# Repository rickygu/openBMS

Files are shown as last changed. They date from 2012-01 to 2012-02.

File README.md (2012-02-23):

Intro
===========

**openBMS is seeking contributors**

Offical Development Google Group: http://groups.google.com/group/openbms

openBMS is an electric vehicle lithium ion battery management system(BMS) based on the [Linear Tech LTC6802-2](http://www.linear.com/product/LTC6802-2) integrated IC and [Cinch ModICE](http://www.cinch.com/products/transportation/modular-integrated-connector-enclosure) automotive enclosure. 

This BMS was originally designed by Ricky Gu of [UBC Electric Car Club](http://ubcecc.com) for the eBeetle project in spring 2010. The eBeetle became the [first electric vehicle to drive coast to coast across Canada](http://www.wired.com/autopia/2010/09/electrified-beetle-goes-coast-to-coast-in-canada/) in summer 2010. This BMS was one of the key component that enabled the eBeetle to drive 6400km in 14 days. 

Todo
==========
* Complete Arduino breakout board to interface with BMS boards
* Start Wiki Documentations

Master Board Features
===============

* Arduino Micro-controller
* Low Voltage Protection
* High Voltage Protection
* LCD Display
* Hall Effect Isolated Current Sensor
* Coulomb Counting

Daughter Board Features
===========

* Measures up to 12 Li-Ion Cells in Series (60V Max)
* Stackable Architecture Enables >1000V Systems
* 0.25% Maximum Total Measurement Error
* 13ms to Measure All Cells in a System
* Cell Balancing:
* On-Chip Passive Cell Balancing
* Two Thermistor Inputs Plus On-Board Temperature Sensor
* 1MHz Daisy-Chainable Serial Interface
* High EMI Immunity
* Delta Sigma Converter with Built-In Noise Filter
* Open Wire Connection Fault Detection
* Low Power Modes

Mechanical Features
===========
* Interfaces with Cinch SHS Harness Connector
* Header modularity and blank headers offer design flexibility for alternate interconnects
* Simple Assembly
* Slide Header/PCB assembly in the Enclosure and snap shut
* Housings – Glass filled polymer
* Pins – Brass – Post tin plated
* Seals – Silicone elastomer
* RoHS – Compliant
* Operating Temperature -55oC to +85oC
* Sealing IP67, IP69K
* Current Cycling 500 Hr
* Salt Fog 96 Hr
* Thermal Shock 10 cycles
* Vibration 10 to 2000 Hz – 20 g peak level – XYZ – 24 Hr
* Shock 50 g – 20 pulses
* Temperature Humidity 1008 Hr
* Temperature Life 1000 Hr
* UV exposure 1000 Hr
* Resists to most fluids used in industrial applications
  
Photos
===========
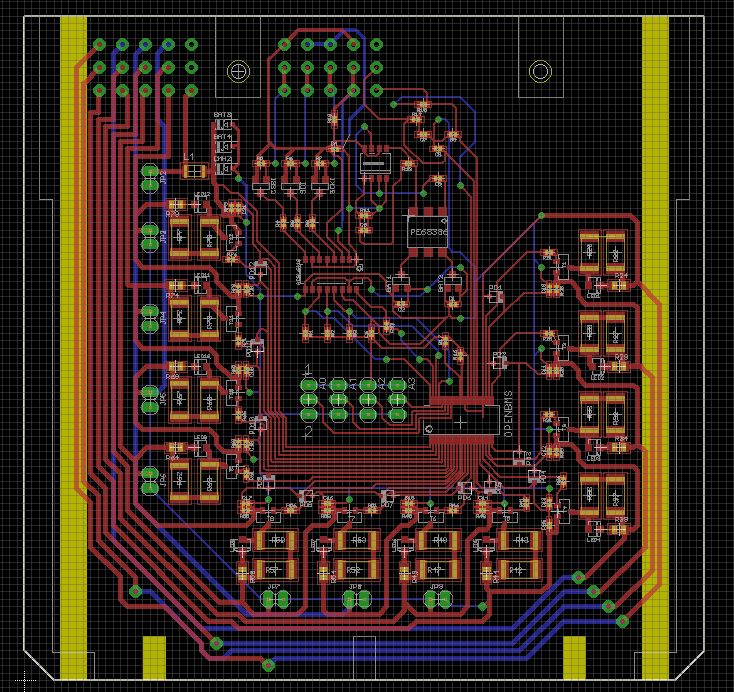
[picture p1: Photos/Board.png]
board

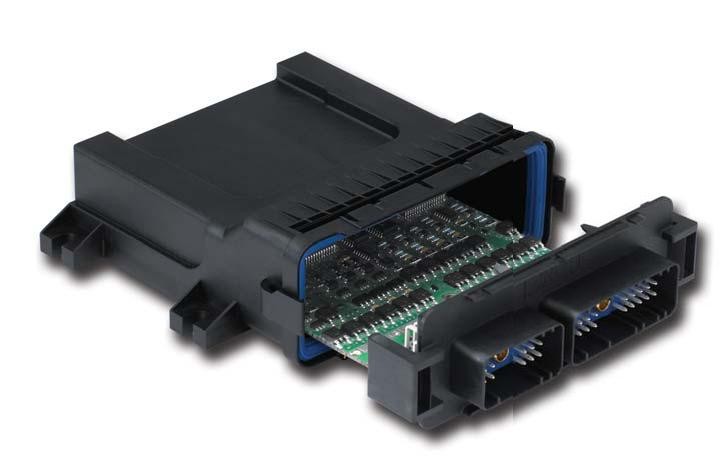
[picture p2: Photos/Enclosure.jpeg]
enclosure

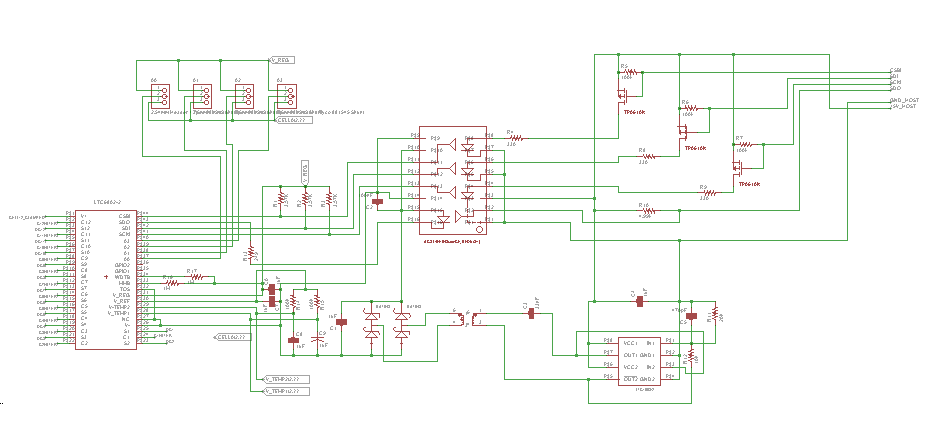
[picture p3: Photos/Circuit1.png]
circuit1

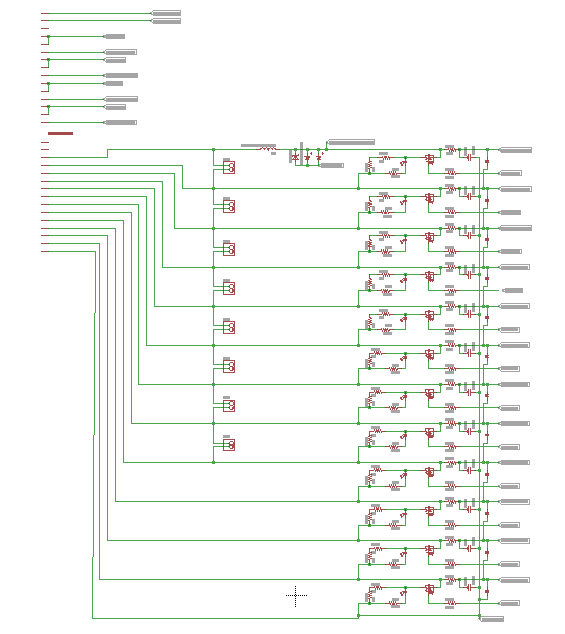
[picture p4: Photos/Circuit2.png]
circuit2


License
===========
This project is released under Creative Commons Noncommercial Share-Alike license.

THE SOFTWARE IS PROVIDED "AS IS", WITHOUT WARRANTY OF ANY KIND, EXPRESS OR IMPLIED, INCLUDING BUT NOT LIMITED TO THE WARRANTIES OF MERCHANTABILITY, FITNESS FOR A PARTICULAR PURPOSE AND NONINFRINGEMENT. IN NO EVENT SHALL THE AUTHORS OR COPYRIGHT HOLDERS BE LIABLE FOR ANY CLAIM, DAMAGES OR OTHER LIABILITY, WHETHER IN AN ACTION OF CONTRACT, TORT OR OTHERWISE, ARISING FROM, OUT OF OR IN CONNECTION WITH THE SOFTWARE OR THE USE OR OTHER DEALINGS IN THE SOFTWARE.

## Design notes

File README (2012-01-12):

openBMS is a lithium ion battery management system(BMS) based on the Linear Tech LTC6802-2 integrated IC and Cinch ModICE automotive enclosure. 

This BMS was originally designed by Ricky Gu of UBC Electric Car Club for the eBeetle project in spring 2010. The eBeetle became the first electric vehicle to drive coast to coast across Canada in summer 2010. This BMS was one of the key component that enabled the eBeetle to drive 6400km in 14 days. 

This project is released under Creative Commons Noncommercial Share-Alike license.

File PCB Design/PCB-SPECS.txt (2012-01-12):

PCB material: FR4, 
1.6mm thickness, 
Pb free HASL, 
solder mask green 
white silkscreen

*All capacitors are 10%

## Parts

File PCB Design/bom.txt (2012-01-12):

Partlist exported from C:/Users/Ricky/Documents/eagle/XBMS3/bms3_1.sch at 28/09/2010 1:58:56 PM

Part     Value                             Device     Package        Description                       
A0       2.54mm Header + Tyco 881545 Shunt PINHD-1X3  1X03           PIN HEADER                        
A1       2.54mm Header + Tyco 881545 Shunt PINHD-1X3  1X03           PIN HEADER                        
A2       2.54mm Header + Tyco 881545 Shunt PINHD-1X3  1X03           PIN HEADER                        
A3       2.54mm Header + Tyco 881545 Shunt PINHD-1X3  1X03           PIN HEADER                        
ACSL6410 ACSL-6410                         ACSL-6410  ACSL-6410-SO16                                   
BAT1     BAT54S                            BAT54S     SOT-23                                           
BAT2     BAT54S                            BAT54S     SOT-23                                           
BAT3     BAT46W                            BAT46W     SOD123         BAT46W Small singla Schottky Diode
BAT4     BAT46W                            BAT46W     SOD123         BAT46W Small singla Schottky Diode
"C1       1uF                               C-EUC0402  C0402          CAPACITOR, European symbol        "
"C2       100nF                             C-EUC0402  C0402          CAPACITOR, European symbol        "
"C3       33nF                              C-EUC0402  C0402          CAPACITOR, European symbol        "
"C4       1uF                               C-EUC0402  C0402          CAPACITOR, European symbol        "
"C5       470pF                             C-EUC0402  C0402          CAPACITOR, European symbol        "
"C6       1uF                               C-EUC0402  C0402          CAPACITOR, European symbol        "
"C7       1uF                               C-EUC0402  C0402          CAPACITOR, European symbol        "
"C8       1uF                               C-EUC0402  C0402          CAPACITOR, European symbol        "
"C9       1uF                               C-EUC0402  C0402          CAPACITOR, European symbol        "
"C10      100n                              C-EUC0402  C0402          CAPACITOR, European symbol        "
"C11      100n                              C-EUC0402  C0402          CAPACITOR, European symbol        "
"C12      100n                              C-EUC0402  C0402          CAPACITOR, European symbol        "
"C13      100n                              C-EUC0402  C0402          CAPACITOR, European symbol        "
"C14      100n                              C-EUC0402  C0402          CAPACITOR, European symbol        "
"C15      100n                              C-EUC0402  C0402          CAPACITOR, European symbol        "
"C16      100n                              C-EUC0402  C0402          CAPACITOR, European symbol        "
"C17      100n                              C-EUC0402  C0402          CAPACITOR, European symbol        "
"C18      100n                              C-EUC0402  C0402          CAPACITOR, European symbol        "
"C19      100n                              C-EUC0402  C0402          CAPACITOR, European symbol        "
"C20      100n                              C-EUC0402  C0402          CAPACITOR, European symbol        "
"C21      100n                              C-EUC0402  C0402          CAPACITOR, European symbol        "
CELL5                                      PINHD-1X2  1X02           PIN HEADER                        
CELL6                                      PINHD-1X2  1X02           PIN HEADER                        
CELL7                                      PINHD-1X2  1X02           PIN HEADER                        
CELL8                                      PINHD-1X2  1X02           PIN HEADER                        
CELL9                                      PINHD-1X2  1X02           PIN HEADER                        
CELL10                                     PINHD-1X2  1X02           PIN HEADER                        
CELL11                                     PINHD-1X2  1X02           PIN HEADER                        
CELL12                                     PINHD-1X2  1X02           PIN HEADER                        
CMHZ     CMHZ5265B                         CMHZ5265B  SOD123                                           
CSBI     TP0610K                           TP0610K    SOT-23                                           
"L1       BLM31PG330SN1L                    L-USL3216C L3216C         INDUCTOR, American symbol         "
LED1     LED-0805                          LED-0805   0805           Green 2V 20mA SMT diode           
LED2     LED-0805                          LED-0805   0805           Green 2V 20mA SMT diode           
LED3     LED-0805                          LED-0805   0805           Green 2V 20mA SMT diode           
LED4     LED-0805                          LED-0805   0805           Green 2V 20mA SMT diode           
LED5     LED-0805                          LED-0805   0805           Green 2V 20mA SMT diode           
LED6     LED-0805                          LED-0805   0805           Green 2V 20mA SMT diode           
LED7     LED-0805                          LED-0805   0805           Green 2V 20mA SMT diode           
LED8     LED-0805                          LED-0805   0805           Green 2V 20mA SMT diode           
LED9     LED-0805                          LED-0805   0805           Green 2V 20mA SMT diode           
LED10    LED-0805                          LED-0805   0805           Green 2V 20mA SMT diode           
LED11    LED-0805                          LED-0805   0805           Green 2V 20mA SMT diode           
LED12    LED-0805                          LED-0805   0805           Green 2V 20mA SMT diode           
LTC1693  LTC1693-2                         LTC1693-2  S8-LTC1693-2                                     
MODICE   MODICE_30                         MODICE_30  CINCH_HEADER30 Cinch MODice 30 enclosure header  
PD1      PDZ7.5B                           PDZ7.5B    SOD323                                           
PD2      PDZ7.5B                           PDZ7.5B    SOD323                                           
PD3      PDZ7.5B                           PDZ7.5B    SOD323                                           
PD4      PDZ7.5B                           PDZ7.5B    SOD323                                           
PD5      PDZ7.5B                           PDZ7.5B    SOD323                                           
PD6      PDZ7.5B                           PDZ7.5B    SOD323                                           
PD7      PDZ7.5B                           PDZ7.5B    SOD323                                           
PD8      PDZ7.5B                           PDZ7.5B    SOD323                                           
PD9      PDZ7.5B                           PDZ7.5B    SOD323                                           
PD10     PDZ7.5B                           PDZ7.5B    SOD323                                           
PD11     PDZ7.5B                           PDZ7.5B    SOD323                                           
PD12     PDZ7.5B                           PDZ7.5B    SOD323                                           
PE68386  PE68386                           PE68386    PE68386                                          
"R1       3.57K                             R-US_R0402 R0402          RESISTOR, American symbol         "
"R2       3.57K                             R-US_R0402 R0402          RESISTOR, American symbol         "
"R3       3.57K                             R-US_R0402 R0402          RESISTOR, American symbol         "
"R4       330                               R-US_R0402 R0402          RESISTOR, American symbol         "
"R5       100k                              R-US_R0402 R0402          RESISTOR, American symbol         "
"R6       100k                              R-US_R0402 R0402          RESISTOR, American symbol         "
"R7       100k                              R-US_R0402 R0402          RESISTOR, American symbol         "
"R8       330                               R-US_R0402 R0402          RESISTOR, American symbol         "
"R9       330                               R-US_R0402 R0402          RESISTOR, American symbol         "
"R10      4.99k                             R-US_R0402 R0402          RESISTOR, American symbol         "
"R11      20k                               R-US_R0402 R0402          RESISTOR, American symbol         "
"R12      10k                               R-US_R0402 R0402          RESISTOR, American symbol         "
"R13      249                               R-US_R0402 R0402          RESISTOR, American symbol         "
"R14      100k                              R-US_R0402 R0402          RESISTOR, American symbol         "
"R15      100k                              R-US_R0402 R0402          RESISTOR, American symbol         "
"R16      1M                                R-US_R0402 R0402          RESISTOR, American symbol         "
"R17      1M                                R-US_R0402 R0402          RESISTOR, American symbol         "
"R20      100                               R-US_R0402 R0402          RESISTOR, American symbol         "
"R21      3.3k                              R-US_R0402 R0402          RESISTOR, American symbol         "
"R22      10                                R-US_R2512 R2512          RESISTOR, American symbol         "
"R23      10                                R-US_R2512 R2512          RESISTOR, American symbol         "
"R24      180                               R-US_R0805 R0805          RESISTOR, American symbol         "
"R25      100                               R-US_R0402 R0402          RESISTOR, American symbol         "
"R26      3.3k                              R-US_R0402 R0402          RESISTOR, American symbol         "
"R27      10                                R-US_R2512 R2512          RESISTOR, American symbol         "
"R28      10                                R-US_R2512 R2512          RESISTOR, American symbol         "
"R29      180                               R-US_R0805 R0805          RESISTOR, American symbol         "
"R30      100                               R-US_R0402 R0402          RESISTOR, American symbol         "
"R31      3.3k                              R-US_R0402 R0402          RESISTOR, American symbol         "
"R32      10                                R-US_R2512 R2512          RESISTOR, American symbol         "
"R33      10                                R-US_R2512 R2512          RESISTOR, American symbol         "
"R34      180                               R-US_R0805 R0805          RESISTOR, American symbol         "
"R35      100                               R-US_R0402 R0402          RESISTOR, American symbol         "
"R36      3.3k                              R-US_R0402 R0402          RESISTOR, American symbol         "
"R37      10                                R-US_R2512 R2512          RESISTOR, American symbol         "
"R38      10                                R-US_R2512 R2512          RESISTOR, American symbol         "
"R39      180                               R-US_R0805 R0805          RESISTOR, American symbol         "
"R40      100                               R-US_R0402 R0402          RESISTOR, American symbol         "
"R41      3.3k                              R-US_R0402 R0402          RESISTOR, American symbol         "
"R42      10                                R-US_R2512 R2512          RESISTOR, American symbol         "
"R43      10                                R-US_R2512 R2512          RESISTOR, American symbol         "
"R44      180                               R-US_R0805 R0805          RESISTOR, American symbol         "
"R45      100                               R-US_R0402 R0402          RESISTOR, American symbol         "
"R46      3.3k                              R-US_R0402 R0402          RESISTOR, American symbol         "
"R47      10                                R-US_R2512 R2512          RESISTOR, American symbol         "
"R48      10                                R-US_R2512 R2512          RESISTOR, American symbol         "
"R49      180                               R-US_R0805 R0805          RESISTOR, American symbol         "
"R50      100                               R-US_R0402 R0402          RESISTOR, American symbol         "
"R51      3.3k                              R-US_R0402 R0402          RESISTOR, American symbol         "
"R52      10                                R-US_R2512 R2512          RESISTOR, American symbol         "
"R53      10                                R-US_R2512 R2512          RESISTOR, American symbol         "
"R54      180                               R-US_R0805 R0805          RESISTOR, American symbol         "
"R55      100                               R-US_R0402 R0402          RESISTOR, American symbol         "
"R56      3.3k                              R-US_R0402 R0402          RESISTOR, American symbol         "
"R57      10                                R-US_R2512 R2512          RESISTOR, American symbol         "
"R58      10                                R-US_R2512 R2512          RESISTOR, American symbol         "
"R59      180                               R-US_R0805 R0805          RESISTOR, American symbol         "
"R60      100                               R-US_R0402 R0402          RESISTOR, American symbol         "
"R61      3.3k                              R-US_R0402 R0402          RESISTOR, American symbol         "
"R62      10                                R-US_R2512 R2512          RESISTOR, American symbol         "
"R63      10                                R-US_R2512 R2512          RESISTOR, American symbol         "
"R64      180                               R-US_R0805 R0805          RESISTOR, American symbol         "
"R65      100                               R-US_R0402 R0402          RESISTOR, American symbol         "
"R66      3.3k                              R-US_R0402 R0402          RESISTOR, American symbol         "
"R67      10                                R-US_R2512 R2512          RESISTOR, American symbol         "
"R68      10                                R-US_R2512 R2512          RESISTOR, American symbol         "
"R69      180                               R-US_R0805 R0805          RESISTOR, American symbol         "
"R70      100                               R-US_R0402 R0402          RESISTOR, American symbol         "
"R71      3.3k                              R-US_R0402 R0402          RESISTOR, American symbol         "
"R72      10                                R-US_R2512 R2512          RESISTOR, American symbol         "
"R73      10                                R-US_R2512 R2512          RESISTOR, American symbol         "
"R74      180                               R-US_R0805 R0805          RESISTOR, American symbol         "
"R75      100                               R-US_R0402 R0402          RESISTOR, American symbol         "
"R76      3.3k                              R-US_R0402 R0402          RESISTOR, American symbol         "
"R77      10                                R-US_R2512 R2512          RESISTOR, American symbol         "
"R78      10                                R-US_R2512 R2512          RESISTOR, American symbol         "
"R79      180                               R-US_R0805 R0805          RESISTOR, American symbol         "
SCKI     TP0610K                           TP0610K    SOT-23                                           
SDI      TP0610K                           TP0610K    SOT-23                                           
T1       RTR020P02                         RTR020P02  TSMT3                                            
T2       RTR020P02                         RTR020P02  TSMT3                                            
T3       RTR020P02                         RTR020P02  TSMT3                                            
T4       RTR020P02                         RTR020P02  TSMT3                                            
T5       RTR020P02                         RTR020P02  TSMT3                                            
T6       RTR020P02                         RTR020P02  TSMT3                                            
T7       RTR020P02                         RTR020P02  TSMT3                                            
T8       RTR020P02                         RTR020P02  TSMT3                                            
T9       RTR020P02                         RTR020P02  TSMT3                                            
T10      RTR020P02                         RTR020P02  TSMT3                                            
T11      RTR020P02                         RTR020P02  TSMT3                                            
T12      RTR020P02                         RTR020P02  TSMT3                                            
X-BMS    LTC6802-2                         LTC6802-2  SSOP-44

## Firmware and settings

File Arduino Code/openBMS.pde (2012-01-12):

#include <Spi.h>
#include <SoftwareSerial.h>

// X-BMS Controller Software Version 1.10
// LTC6802-2 in addressable mode

//For UBCECC E-Beetle 
// 32 Cell LiFePO4 480AH Thundersky
// 3 x daughter board with address set at 0000 / 0001 / 0010


// Written by Ricky Gu 

//March 5 11

// BMS Settings
#define BOTTOMSTACK   0x80 // bottom bms board address 0000
#define TOPSTACK      0x82 // set bms to 3 daughter boards with top of stack address of 0010
#define TOTALCELLS    32   // Set total cell number to 32
#define TOTALBOARDS   3    // set total board number to 3
#define HIGHVOLTAGECUTOFF 3.7  // Define high voltage cut off
#define LOWVOLTAGEWARNING 2.8  // Define low voltage warning
#define LOWVOLTAGECUTOFF 2.55   // Define low voltage cut off
#define VOLTAGEALLOWANCE 0.009 // Define the accuracy the balancing algorithm can balance it to.
#define CURRENTSENSOR 0 //Define the pin which the current sensor reading is in
#define DELTASIGMAFACTOR 30 //define delta sigma adc factor
#define ADCREFERENCEVOLTAGE 3.3 //use external adc reference voltage of 3.3v
#define CHARGERSHUTOFF 8
#define BATTERYSHUTOFF 9
#define GENERALRELAY 7
#define CHARGERRESTARTVOLTAGE 3.5
#define LCDPIN 3
#define RESETPIN 2 
#define HIVOLTAGESHUNT 3.5
// Definition of all constants

#define TALK digitalWrite(SS_PIN, LOW); // Chip Select
#define DONE digitalWrite(SS_PIN, HIGH); // Chip Deselect


// LTC6802-2 Command Codes 

#define WRCFG  0x01  // Write Configuration Registers
#define RDCFG  0x02  // Read Configuration 
#define RDCV   0x04  // Read Cell Voltages without discharge

#define RDFLG  0x06  // Read Flags
#define RDTMP  0x08  // Read Temps

#define STCVAD 0x10  // Start all A/D's - Poll Status
#define STCVDC 0x60  // A/D Conversions and Poll Status, with Discharge Permitted
#define STOWAD 0x20  // Start testing all open wire - poll status
#define STTMPAD 0x30 // Start temperature A/D's - Poll Status


// Function Declaration
void wakeUp();
void readVolts();
float vTotal();
float vAvg();
int highestCell();
int lowestCell();
void balanceCells();
void writeConfig();
void readCurrent();
void selectLineOne();
void selectLineTwo();
void clearLCD();
void goTo(int position);
void updateServer();

// Variable declaration 
byte ltcResponse[20];
float voltage[12*TOTALBOARDS+1];
float cellVoltage[TOTALCELLS+1];
int evenCell;
int intTemp;
byte byteTemp;
byte address;
float voltageTotal;
float voltageAverage;
float voltageHighest;
float voltageLowest;
int highestCellNumber;
int lowestCellNumber;
boolean isCellTooHigh;
boolean isCellTooLow;
boolean isCellWayTooLow;
byte CFGR1 = 0;
byte CFGR2 = 0;
int cellToSend;
int zeroReference;
int instantCurrent;
SoftwareSerial LCD = SoftwareSerial(0, LCDPIN);  
int LCDvoltage;
int LCDlowcell;
int LCDhighcell; 
double mVhighest;
double mVlowest; 
float watt;
float wattHour;
unsigned long previousTime;
unsigned long currentTime;
float deltaTime;
boolean reset;
int regen;
int isChargingCounter;
int isCharging;
boolean printLCD;
long Wh;
int Percent;


void setup()
{
  // SPI configuration
  // No interupt, Enable SPI, MSB first, Master, Clock rests high
  // read on rising edge, 1mhz speed

  DONE // Set CS High
  pinMode(RESETPIN, INPUT);
  digitalWrite(RESETPIN, HIGH);
  pinMode(CHARGERSHUTOFF, OUTPUT);
  pinMode(BATTERYSHUTOFF, OUTPUT);
  pinMode(GENERALRELAY, OUTPUT);
  Spi.mode ((1<<SPE) | (1<<MSTR) | (1<<CPOL) | (1 << CPHA)| (1 << SPR1) | (1<<SPR0) );
  Serial.begin(9600);
  //Serial.print("\e[2J");
  zeroReference = 0;
  analogReference(EXTERNAL);
  for(int i = 0; i < DELTASIGMAFACTOR; i ++)
  {
    zeroReference = zeroReference + analogRead(CURRENTSENSOR);
  }
  zeroReference = zeroReference/DELTASIGMAFACTOR;
  pinMode(LCDPIN, OUTPUT);
  LCD.begin(9600);
  clearLCD();
  wattHour  = 0;
  previousTime = 0;
  currentTime= 0;
  isChargingCounter = 0;
  isCharging = 0;
  // lcdPrint = true;
}


void loop(){
  //reset e-meter
  reset = digitalRead(RESETPIN);
  if(reset == LOW)
  {
    wattHour = 0;
    clearLCD();
  }

  // Start A-D, Read Current (not implemented yet), Save voltages into cellVoltage Array
  //wakeUp();

  readVolts();

  // Read Current Transducer
  readCurrent();

  // calculate total and average voltage of battery pack
  voltageTotal = vTotal();
  voltageAverage = voltageTotal / TOTALCELLS;

  //calculate power and record energy useage
  watt = voltageTotal * instantCurrent;
  previousTime = currentTime;
  currentTime = millis();
  deltaTime = (currentTime - previousTime);

  wattHour = wattHour + watt*deltaTime/3600000;
  Wh = (long) wattHour;

  //Serial.print(deltaTime);

  Serial.print("Total Voltage:");
  Serial.print(voltageTotal);
  Serial.print("   Average V");
  Serial.println(voltageAverage);
  

  // Locate the highest voltage cell number. Highest voltage cell value located in float voltageHighest

  highestCellNumber = highestCell();
  /*
Serial.print("highest cell: ");
   Serial.print(highestCellNumber);
   Serial.print(" is ");
   Serial.print(voltageHighest);
   Serial.println(" V");
   */


  // is cell higher than high voltage cutoff?

  if(voltageHighest >= HIGHVOLTAGECUTOFF)
  {
    isCellTooHigh = true; 
    digitalWrite(CHARGERSHUTOFF, HIGH);
  }
  else
  {
    isCellTooHigh = false;
    if(voltageHighest < CHARGERRESTARTVOLTAGE)
    {
      digitalWrite(CHARGERSHUTOFF, LOW);
    }
  }

  // locate the lowest voltage cell

  lowestCellNumber = lowestCell();

  /*
Serial.print("lowest cell: ");
   Serial.print(lowestCellNumber);
   Serial.print(" is ");
   Serial.print(voltageLowest);
   Serial.println(" V");
   */
  //Check if it's charging
  if(instantCurrent < 0)
  {
    isChargingCounter++;
  }
  else
  {
    isChargingCounter = 0;
  }

  if(isChargingCounter > 300)
  {
    isCharging = 1;
  }
  else
  {
    isCharging = 0;
  }

  if (printLCD = true)
  {
    selectLineOne();
    //LCD.print("V:");
    //LCDvoltage = (int) voltageTotal;
    //LCD.print(LCDvoltage);
    LCD.print("E:");
    LCD.print(Wh);
    LCD.print(" ");
    goTototal(9);
    LCD.print(" A:");
    LCD.print(instantCurrent);
    LCD.print("  ");
    selectLineTwo();
    mVlowest = voltageLowest *100;
    LCDlowcell = (int)mVlowest;
    LCD.print("L");
    LCD.print(lowestCellNumber);
    LCD.print(':');
    LCD.print(LCDlowcell);
    goTo(24);
    LCD.print(" H");
    LCD.print(highestCellNumber);
    LCD.print(':');
    mVhighest = voltageHighest*100;
    LCDhighcell = (int) mVhighest;
    LCD.print(LCDhighcell);
    printLCD = !printLCD;
  }

  // is this cell lower than 3.0V? if so warn driver

  if(voltageLowest < LOWVOLTAGEWARNING)
  {
    isCellTooLow = true;
    //warn driver here
    // is this cell lower than 2.8v? cut battery pack if kwh remaining is under 3kwh. 

    if(voltageLowest < LOWVOLTAGECUTOFF)
    {
      isCellWayTooLow = true;
      if(instantCurrent < 30)
      {
        digitalWrite(BATTERYSHUTOFF, HIGH);
      }
      //Serial.print("cell too low");
      //digitalWrite(BATTERYSHUTOFF, HIGH);
      //Check Kwh and cut battery pack here
    }
    else
    {
      isCellWayTooLow = false;
    }
  }
  else
  {
    isCellTooLow = false;
    // find cells that are above the lowest voltage cell by the defined VOLTAGEALLOWANCE value. 


  }

  // turn on shunt resistors on the cells that are 0.05v higher than the average
  // turn off the rest
  balanceCells();

  // display data on LCD

  // send data to web server



}

void wakeUp()
{
  TALK
    Spi.transfer(0x01);   // Command Set
  Spi.transfer(0xE2);   // Command Wake up
  Spi.transfer(CFGR1);   // Command
  Spi.transfer(CFGR2);   // Command
  Spi.transfer(0x00);   // Command
  Spi.transfer(0x00);   // Command
  Spi.transfer(0x00);   // Command
  DONE
}
void readVolts()
{
  // Broadcast Command, start A-D
  TALK
    Spi.transfer(STCVAD);
  //delay(20); // wait 20ms for all the boards to read ADC (use this delay time to read current)
  //send cell voltage to fill delay


  //ansi escape code to clear screen
  //Serial.println("\e[0;0H");
  if(Serial.available() > 0)
  {
    updateServer();
  }
  else
  {
    delay(20);
  }

  DONE

    address = BOTTOMSTACK;

  for(int boardNumber = 0; boardNumber < TOTALBOARDS; boardNumber++)
  {
    //Serial.print("address:");
    //Serial.println(address, HEX);
    // Read 18 byte from 1 board and then increment address to read the next
    TALK
      Spi.transfer(address);
    Spi.transfer(RDCV);
    for(int i=0; i<19; i++)
      ltcResponse[i] = Spi.transfer(RDCV);   // send command to read voltage registers
    DONE

      for (int i=1; i<=12; i++)
    {
      int x = i + 12*boardNumber; 
      //Serial.println(x);
      if(i == 1)
      {
        byteTemp = ltcResponse[1] << 4;
        intTemp = (int)byteTemp;
        voltage[x] = ltcResponse[0] + (intTemp << 4);
      }
      if(i== 2)
      {
        byteTemp = ltcResponse[1] >> 4;
        intTemp = (int)ltcResponse[2];
        intTemp = intTemp << 4;
        voltage[x] = intTemp + byteTemp;
      }
      if(i == 3)
      {
        byteTemp = ltcResponse[4] << 4;
        intTemp = (int)byteTemp;
        voltage[x] = ltcResponse[3] + (intTemp << 4);
      }
      if(i== 4)
      {
        byteTemp = ltcResponse[4] >> 4;
        intTemp = (int)ltcResponse[5];
        intTemp = intTemp << 4;
        voltage[x] = intTemp + byteTemp;
      }
      if(i == 5)
      {
        byteTemp = ltcResponse[7] << 4;
        intTemp = (int)byteTemp;
        voltage[x] = ltcResponse[6] + (intTemp << 4);
      }
      if(i== 6)
      {
        byteTemp = ltcResponse[7] >> 4;
        intTemp = (int)ltcResponse[8];
        intTemp = intTemp << 4;
        voltage[x] = intTemp + byteTemp;
      }
      if(i == 7)
      {
        byteTemp = ltcResponse[10] << 4;
        intTemp = (int)byteTemp;
        voltage[x] = ltcResponse[9] + (intTemp << 4);
      }
      if(i== 8)
      {
        byteTemp = ltcResponse[10] >> 4;
        intTemp = (int)ltcResponse[11];
        intTemp = intTemp << 4;
        voltage[x] = intTemp + byteTemp;
      }
      if(i == 9)
      {
        byteTemp = ltcResponse[13] << 4;
        intTemp = (int)byteTemp;
        voltage[x] = ltcResponse[12] + (intTemp << 4);
      }
      if(i== 10)
      {
        byteTemp = ltcResponse[13] >> 4;
        intTemp = (int)ltcResponse[14];
        intTemp = intTemp << 4;
        voltage[x] = intTemp + byteTemp;
      }
      if(i == 11)
      {
        byteTemp = ltcResponse[16] << 4;
        intTemp = (int)byteTemp;
        voltage[x] = ltcResponse[15] + (intTemp << 4);
      }
      if(i== 12)
      {
        byteTemp = ltcResponse[16] >> 4;
        intTemp = (int)ltcResponse[17];
        intTemp = intTemp << 4;
        voltage[x] = intTemp + byteTemp;
      }
    }
    //Serial.print("Board Number:");
    //Serial.println(boardNumber);
    address++;
  }
  //decode register into voltage values. 
  for(int i = 1; i <= TOTALCELLS; i++)
  {
    cellVoltage[i] = voltage[i] * 1.5 / 1000;
    //if(instantCurrent > 10)
    //cellVoltage[5] += instantCurrent*0.0015;
    /*
      Serial.print("C");
     Serial.print(i);
     //Serial2.println(i);
     Serial.print(": ");
     Serial.print(cellVoltage[i]);
     Serial.print(";  ");
     //Serial2.println(cellVoltage[i]);
     */
    /*
      if(i == 6) Serial.println(' ');
     if(i == 12) Serial.println(' ');
     if(i == 18) Serial.println(' ');
     if(i == 24) Serial.println(' ');
     if(i == 30) Serial.println(' ');
     */
  }
  //Serial.println(' ');
}

float vTotal(){
  float total = 0;
  for (int i = 1; i <= TOTALCELLS; i++){
    total = total + cellVoltage[i];
  }
  return total;
}

int highestCell()
{
  voltageHighest = 0;
  int cellNumber;
  for (int i = 1; i <= TOTALCELLS; i++)
  {
    if (cellVoltage[i] > voltageHighest)
    {
      voltageHighest = cellVoltage[i];
      cellNumber = i;
    }
  }
  return cellNumber;
}

int lowestCell()
{
  voltageLowest = 99;
  int cellNumber;
  for(int i = 1; i <= TOTALCELLS; i++)
  {
    if (cellVoltage [i] < voltageLowest)
    {
      voltageLowest = cellVoltage[i];
      cellNumber = i;
    }
  }
  return cellNumber;
}

void balanceCells()
{
  CFGR1 = 0x00;
  CFGR2 = 0x00;
  byte temp;
  int x;
  address = BOTTOMSTACK;
  float difference[TOTALCELLS];

  //find difference and save in an array
  for(int i = 1; i<= TOTALCELLS; i++)
  {
    difference[i] = cellVoltage[i] - HIVOLTAGESHUNT;
    /*
      Serial.print("cell");
     Serial.print(i);
     Serial.print("difference is: ");
     Serial.println(difference[i]);
     */
  }

  for(int boardNumber = 0; boardNumber < TOTALBOARDS; boardNumber++)
  {
    CFGR1 = 0x00;
    CFGR2 = 0x00;
    if(isCellTooLow == true)
    {
      CFGR1 = 0x00;
      CFGR2 = 0x00;       
    }
    else
    {
      for(int i = 1; i <= 12; i++) 
      {
        int cellNumber = i + (boardNumber*12);
        if(i <= 8)
        {
          if(difference[cellNumber] > VOLTAGEALLOWANCE)
          {
            x = i - 1; // calculate position to shift
            temp = 0x01;
            temp = temp << x;
            CFGR1 = CFGR1 + temp; // bitwise or
            /*
                  Serial.print("Cell ");
             Serial.print(cellNumber);
             Serial.print("should be shunt");
             Serial.print("CFGR1 is");
             Serial.println(CFGR1, HEX);
             */
          }
        }
        else
        {
          if(difference[cellNumber] > VOLTAGEALLOWANCE)
          {
            x = i - 9;
            temp = 0x01;
            temp = temp << x;
            CFGR2 = CFGR2 + temp;
            /*
                  Serial.print("Cell ");
             Serial.print(cellNumber);
             Serial.print("should be shunt");
             Serial.print("CFGR2 is");
             Serial.println(CFGR2, HEX);
             */
          }
        }
      }
    }
    writeConfig();
    address++;

  }

}

void writeConfig()
{
  TALK
    Spi.transfer(address);   // Command addresss
  Spi.transfer(0x01);   // Commandwrite CRG
  Spi.transfer(0x01);   // WRITE CFGR0 
  Spi.transfer(CFGR1);   // WRITE CFGR1 
  Spi.transfer(CFGR2);   // WRITE CFGR2
  Spi.transfer(0x00);   // WRITE CFGR3
  Spi.transfer(0x00);   // WRITE CFGR4
  Spi.transfer(0x00);   // WRITE CFGR5
  DONE
}

void readCurrent()
{
  int adc = 0;
  analogReference(EXTERNAL);
  for(int i = 0; i < DELTASIGMAFACTOR; i++)
  {
    adc = adc + analogRead(CURRENTSENSOR);
  }
  adc = adc/DELTASIGMAFACTOR;
  //calculation forumla based on LEM HASS 600-S Current Transducer
  instantCurrent = (adc-zeroReference)*(ADCREFERENCEVOLTAGE/1024)*600/0.625;
  int absCurrent;
  absCurrent = abs(instantCurrent);
  if(absCurrent < 4)
    instantCurrent = 0;

  Serial.print("Current: ");
  Serial.print(instantCurrent);
  Serial.println("Amps");

}

void selectLineOne(){  //puts the cursor at line 0 char 0.
  LCD.print(0xFE, BYTE);   //command flag
  LCD.print(128, BYTE);    //position
}
void selectLineTwo(){  //puts the cursor at line 0 char 0.
  LCD.print(0xFE, BYTE);   //command flag
  LCD.print(192, BYTE);    //position
}
void clearLCD(){
  LCD.print(0xFE, BYTE);   //command flag
  LCD.print(0x01, BYTE);   //clear command.
}
void goTo(int position) { //position = line 1: 0-15, line 2: 16-31, 31+ defaults back to 0
  if (position<16){ 
    LCD.print(0xFE, BYTE);   //command flag
    LCD.print((position+128), BYTE);    //position
  }
  else if (position<32){
    LCD.print(0xFE, BYTE);   //command flag
    LCD.print((position+48+128), BYTE);    //position 
  } 
  else { 
    goTo(0); 
  }
}

void updateServer()
{
  if(Serial.available() > 0)
  {
    cellToSend = Serial.read();
    if(cellToSend == 0)
    {
      Serial.print(wattHour);
    }
    if(cellToSend == 1)
    {
      Serial.print(voltageTotal);
    }
    if(cellToSend == 2)
    {
      Serial.print(instantCurrent);
    }
    if(cellToSend == 3)
    {
      if(instantCurrent < 0)
      {
        regen = abs(instantCurrent);
        Serial.print(regen);
      }
      else
      {
        Serial.print('0');
      }
    }
    if(cellToSend == 4)
    {
      Serial.print(isCharging);
    }

    if(cellToSend >3)
    {
      Serial.print(cellVoltage[cellToSend-4]);
      Serial.flush();
    }
  }
}

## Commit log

2012-01-12 inital commit to git repo
    [bms3.brd, bms3.sch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]
2012-02-23 updated to openBMS logo, clean up unneeded files
    [bms3.brd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]
